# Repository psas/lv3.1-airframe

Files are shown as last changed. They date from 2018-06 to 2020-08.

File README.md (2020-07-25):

# LV3.1 Airframe
Design and testing documents related to the LV3.1 airframe.

## Table of Contents

* [license](#license)
* [cad](#cad)
* [doc](#doc)
* [sim](#sim)
* [test](#test)
* [tools](#test)

## license 
Copyright Portland State Aerospace Society 2018.

This documentation describes Open Hardware and is licensed under the CERN OHL v. 1.2.
You may redistribute and modify this documentation under the terms of the CERN OHL v.1.2. [http://ohwr.org/cernohl](http://ohwr.org/cernohl). 
This documentation is distributed WITHOUT ANY EXPRESS OR IMPLIED WARRANTY, INCLUDING OF MERCHANTABILITY, SATISFACTORY QUALITY AND FITNESS FOR A PARTICULAR PURPOSE. 
Please see the CERN OHL v.1.2 for applicable conditions.

## cad
All the computer aided design (CAD) files involved in the airframe is in this folder. Details of each folder in the directory can be found in the readme section of this directory. Most of our CAD modeling here is done and saved as solidworks files

## doc
This directory contains all the files documents regarding airframe, specifically documentation for layup processes. 

## sim
This directory contains all the simulations for LV3.1, such as rocket simulations.

## test
This directory contains all the testing data for LV3.1, such as any axial load tests performed.

## tools
This directory contains all information regarding generic tooling we use for LV3.1.

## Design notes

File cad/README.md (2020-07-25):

## CAD
This directory contains all our computer aided design (CAD) files. This includes parts, assemblies, drawings, and STEP files. Below is a listing of all the folders in this file and a short description on what they are for. 

* Commercial off the shelf components (COTS)
  - These files are all manufactured provided and not owned by PSAS, however it is in the repo to help clarify PSAS designs.
* Layup templates
  - Templates made to assist in cutting appropiate carbon fiber and nomex layers for modules B and C to aid in the layout process. Design journal can be found [here](https://docs.google.com/document/d/1Os_mgdvX-xlpNA5_TTuyKTH5s2XwF5QlSnMKPRlPtjE/edit?usp=sharing).
* Build
  - Where we put our files before they get machined as an easy place to go to when we want to check what our current physical parts look like. Organizes both the STEP and technical drawings. 
* Bulkheads
  - Directory where all the files related to the bulkhead are. A bulkhead is a dividing barrier between modules. A design journal for the bulkhead can be found [here](https://docs.google.com/document/d/1OEyzK1N2RJoIQbxRXQRS35BUAtLPPHPcPFbIrotuAhM/edit?usp=sharing).
* Coupling
  - Directory which contains all the files regarding to the LV3.1 coupling system used to connect the LV3.1 modules together.
* Fincan
  - Directory contains files describing the fin cannister, such as the bracket for the layup jig, the layup rig. Also includes images. 
* Fins
  - Directory containing all the files regarding our fins.
* Modules
  - Directory containing all files regarding our modules, including composite inner and outer sleeves, coupling examples, and our module rings.
* Nose
  - Short for nosecone, this directory has all the soldiworks files and PDFs contain files describing the LV3.1 nosecone. 
* Passthrough
  - Directory containing files for the passthrough ring for our rocket. This is a module where all the camera mounts will be.
* Rail mount
  - Directory containing files deccribing the system that mounts the rocket to the launch rail.
* Templates
  - Drawing templates (solidworks).
* Thrust flange
  - The thrust flange is the flange that the motor of the rocket will rest against. 
* Airframe bracket jig
  - Step file for the airframe bracket jig.

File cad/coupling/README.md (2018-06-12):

# Coupling System
This directory contains files which define how the LV3.1 modules couple together.

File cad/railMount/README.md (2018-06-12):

# Rail Mount
This directory contains files describing the system that mounts the LV3.1 airframe to the launch rail.

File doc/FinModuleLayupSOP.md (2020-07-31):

# Materials
* Popsicle sticks
* Wax paper
* Epoxy (proglass)
* Stirring Cups (BIG ONES)
* One (small) clamp
* Shop towels
* Gloves
* Isopropyl alcohol
* Hex wrench - 4mm or No. 6
* Foam
* X-acto kit
* Scissors
* Sharpie
* Kapton tape
* Masking tape
* Sand paper (600 grit)
* Spray bottle of water (past day 1)
* Sandbag
* Acrylic
* Abrasive Cleaner(Orange Bottle)
* Scale

# Day One
## Calibration and Prep
1. Sand all inner surfaces of the brackets
2. Find the largest seam on the module (if one exists).
3. Pick the closest bulkhead clamp screw hole.
4. Put module on the rig.
5. Put a sandbag inside the module, about in the middle, to weigh the module down during the process.
6. Using a black sharpie (choose any color, but make sure to use that color when I say black), mark a line on the end of the ring in-line with the arc clamp hole chosen.
7. Rotate the module two bulkhead holes clockwise, mark a line on the end in-line with this hole with a red sharpie (any color other than the one you used before).
8. Repeat step 4, alternating black and red sharpies until you make it back to the first line.
 * The idea behind this is to indicate that the black lines are where the fins line up, and the red lines are used to line up the module with the notches on the jig.
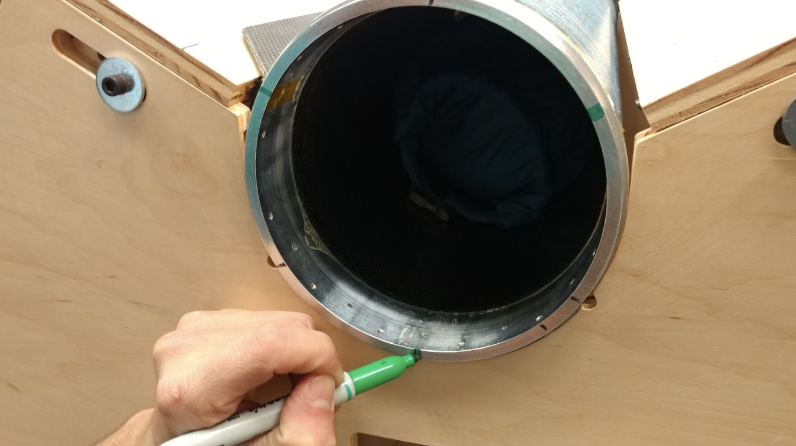
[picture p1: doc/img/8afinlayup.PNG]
 
9. Line up the inside edge of the ring with the inside edge of the front of the rig.
 * The idea is to line up the trailing end of the bracket with the inside edge of the ring module.
10. Line up two of the red lines with the notches on the rig.
  
11. Stick double-sided foam tape on the curved surface of the inside corner of a fin bracket.
12. Press the inside corner on the downward facing edge of the alignment surface of the rig, aligned with the inside edge of the module ring. This end is the bottom of the rocket.
13.Apply kapton tape around all outer module ring surfaces.
14. Move the alignment surfaces so the bracket is lightly pressed up against the module.
15. Draw a line on the module along the bottom edge of the bracket.
  
16. Back the alignment surface off and remove the module
17. Apply wide kapton tape directly underneath the marked line.
18. Tape a sheet wax paper on top of the existing kapton tape.
  * Make sure the wax paper is long enough to wrap around the bottom of the module.
19. Tape down all other edges of the wax paper.
20. Apply more wax paper as needed to span the entire length of the marked line/to wrap around the bottom of the module.
21. Reinsert the module into the jig.
22. Make sure that the module is clamped to the jig.
23. Sanity check! Make sure that the fin bracket doesn’t overlap with kapton tape.

## Layup:
24. Measure out a total of 100 g (50 of A and 50 of B) of epoxy for all surfaces. Instructions for epoxy on bottle.
  * Epoxy will get a little cloudy when fully mixed
25. Apply epoxy to the concave surface of the bracket.

26. Using the alignment surface, press the epoxied bracket onto the module where it was aligned before.
27. Hold a long piece of acrylic onto the curved surface of the bracket, underneath the alignment surfaces.
28. Firmly and evenly screw down the alignment surface bolts onto the piece of acrylic.

29. Wait at least 24 hours for curing.

# DAY 2/DAY 3/DAY 4:
## Calibration and Prep
30. MAKE SURE YOU HAVE GLOVES ON WHEN TOUCHING THE BRACKETS
31. Sand both faces of the fin, approximately the width of the fin backet, using water and sandpaper. Clean with IPA.
32. Carefully separate the alignment surface from the bracket. (Be careful taking out the module.)
  * Use a wedge of some sort to separate the foam tape from the alignment surface if necessary.
33.Remove the foam tape completely from the bracket.
34. Apply double-sided foam tape along the inside faces of TWO brackets.
  * For Day 4, it is in fact, only ONE bracket. Remove non-used alignment surface.
35. Stick the brackets on both alignment surfaces, aligning the brackets the same way as in step 9, but do not press down fully yet.

36. Rotate the module 120°. 
  * Line up the red line with the notch on the rig.
  * The orthogonal surface of the laid-up bracket should be facing downward and slightly above the new bracket.
  * For Day 3 and 4, the module will need to be taken off the rig to rotate
37. Repeat steps 10 through 16 for both sides.
  * Sandwich a fin between two brackets

38. Mark front end of fin on module (as reference)
39. Put Kapton tape along the module, the Kapton tape should be right underneath where the bracket goes
40. Tape a sheet of wax paper on top of the existing kapton tape.
  * Day 2: Make sure the wax paper is long enough to wrap around the module fully between the lines of kapton tape.
  * Day 3/4: Just let the wax paper dangle.
  * Day 4: Only one side is needed.
41. Tape down all other edges of the wax paper.
42. Apply more wax paper as needed to span the entire length of the marked line/to wrap between the lines.
43. Wipe down the exposed faces of the module with isopropyl alcohol 
44. Tape the top face of the fin with masking tape so you move the fin up and down like a flap so the fin stays in the same position.

## Layup:
45. Rotate the module slightly back, giving enough clearance between the old a new bracket for a fin.
46. Measure out a total of 100 g (50 of A and 50 of B) of epoxy for all surfaces. Instructions for epoxy on bottle.
  * Epoxy will get a little cloudy when fully mixed
  * Somewhat less is needed is needed for Day 4
47. Apply epoxy to the exposed surfaces of the brackets.

48. Put bracket into position onto alignment surface
49. Apply epoxy to new bracket mating side of fin
  * Have a shop towel soaked with iso ready to wipe off dripping epoxy

50. Fold fin down onto new bracket and hold firm
51. Epoxy remaining side of fin and the old bracket mating face

52. Rotate fin can until flush with fin
53. Press alignment surface down onto module
54. Line up edges of old to new bracket
55. Sandwich fin as firmly as possible between the two brackets
56. And clamp! 

57. Screw in the sides with the hex wrench
58. Cinch the bracket down with the strap and ratchet. 
59.Seal any extra space between the bracket and the fin with leftover epoxy
60. Put the acrylic on the bottom of the curved part of the bracket and press firm with screws
  * Put wax paper underneath the acrylic 
61. Repeat Day 1 layup for the second bracket
  * Not needed on Day 4

62. Wait at least 24 hours for curing.

# Post Layup Touch Ups:
* Fill any gaps between bracket and fin or bracket and module with epoxy
* Sand, sand, sand
* Clean with isopropyl

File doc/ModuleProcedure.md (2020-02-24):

---
Title: Composites Layup Procedure
Date: \today
Author:
  - Joe Shields
  - Leslie Elwood
  - Alex Farias
Revision: Version 3.1
Revised by:
  - Gabe Paris
Fontsize: 12pt
Documentclass: article
Geometry: margin=0.75in
Numbersections: true
Toc: true
Pagestyle: plain
Output:  
  pdf_document:
    latex_engine: xelatex
---
# Introduction
This is the procedure to make a cylindrical module specifically for the Launch Vehicle (LV) 3.1. If you find any steps that are unclear, erroneous, unneccessary, or need improvement, please [add an issue for it on this repo](https://github.com/psas/lv3.1-airframe/issues).

This procedure takes about 5 hours if you have three people working on it, not counting the 5 hour cure cycle. If you're following this procedure for the first time, it will probably be closer to 7 or 8 hours. If you *really* know what you're doing, one person can do it, but it's not nice to make one person work for 10 hours straight. If you're trying modifications to this procedure, it's a good idea to do so on a smaller mandrel with no coupling rings, since that takes off a lot of the time.

The composites training video can be found here [link coming soon], and it goes over the process of making these modules. If this is your first time following this procedure, please watch the video first.

## Materials
### Consumables
1. [Orca skin](http://www.fiberlay.com/upload/techd-2522041-252204_OrcaSkin_Data.pdf)
1. [Orca seal](http://www.fiberlay.com/upload/techd-252203-252203_OrcaSeal_Data.pdf)
1. Shrink tape
1. Non-perforated release film
1. Vacuum bag sheets
1. Vacuum bagging tape ("goop tape")
1. Vacuum bagging breather material
1. 320 grit sandpaper
1. 600 grit sandpaper
1. 1500 grit sandpaper
1. Acetone
1. Powderless nitrile gloves
1. Blue shop towels
1. Kapton tape or flash tape
1. 1 whole 3M AC-130 pre-treatment solution
1. Separation wax

### Layup Pieces
1. Prepreg carbon fiber (Satin weave is preferable. Anything but unidirectional will do. We use Cytec BMS-8-297 3K-70-PW TY4 CL2, which is the big yellow roll in the EB 480 freezer.)
1. Structural adhesive (We use Cytec's Meltbond 1515-3M, which bonds to CF, nomex, and aluminum. We know that 3M's AF-126 DOES NOT WORK.)
1. Two (Generation 2) Aluminum Coupling Rings
1. 12 aluminum coupling ring arc clamps
1. 1/4" thick over-expanded nomex honeycomb
1. An aluminum mandrel (6.0" OD!)

### Tools
1. Vacuum pump (we use a venturi pump)
1. Air hose
1. Insulated gloves (gardening gloves will work)
1. Utility knife
1. XActo knife (Optional, but helpful for finer trimming.)
1. Scissors
1. Mandrel-to-ring screws (size)
1. A small piece of acrylic (Popsicle sticks will work as well, albeit more difficult)
1. Material templates and weights

# Preparation
The following steps can be done in parallel. If you have the space and the people, this is recommended to save time.
## Mandrel Preparation
#### Mandrel Cleaning
1. Put on powderless nitrile gloves.
1. Use a piece of acrylic or a popsicle stick to scrape away any chunks of epoxy or adhesive currently on the mandrel from the previous layup.
1. Wet sand the mandrel with 320 grit paper to remove the epoxy and adhesive from the previous layup.
1. Wet sand the mandrel with 600 grit paper, removing the marks from the previous sanding.
  1. The sanding direction can be alternated (that is, axial v.s. radial) to better identify any spots that were missed, but this is optional.
1. Wet sand the mandrel with 1500 grit paper, removing the marks from the previous sanding. You want the mandrel to be as smooth as possible before continuing.
1. Put on fresh (as in change to a new pair) powderless nitrile gloves.
1. Wipe the mandrel with acetone and a blue shop towel to clear the sanded epoxy and metal dust until the towel comes back clean.
1. Relocate the mandrel and the composites table to a space with good ventilation. We normally use a spot on the north end of the first floor of EB where there is a set of double doors for ventilation.

#### Mandrel Conditioning
The figure below shows the waxed mandrel along with a container of Orca skin and Orca wax. This should be done in an area with good ventilation because the wax chemicals are very potent.

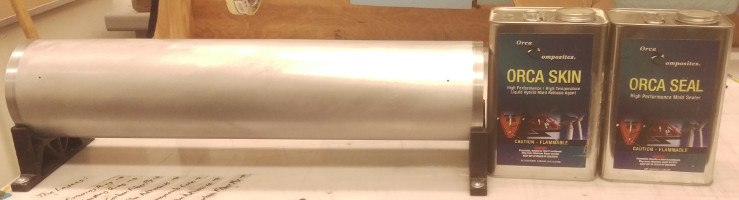
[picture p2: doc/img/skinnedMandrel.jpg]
The waxed mandrel on the preparation table, along with a container of Orca Skin and Orca Seal


1. Put on (Brand new!) powderless nitrile gloves.
1. Place the freshly sanded mandrel to be conditioned on the mandrel holders.
1. Fill mandrel threaded holes with separation wax.
1. Apply 2 coats of Orca Seal. For each coat, complete the following:
   1. Shake the container of Orca seal to mix the wax and then unscrew the lid.
   1. Apply some Orca seal to a blue shop towel by *carefully* covering the opening of the container and briefly inverting.
   1. As lightly as you can and as evenly as you can wipe the wax onto the mandrel. Usually the first wiping motion of the towel will be thick and visible on the mandrel; this is common. If you are able to more evenly distribute the thicker streak, do so, otherwise it will be fine.
   1. If there are any chunks of wax, carefully remove them with a shop towel.
   1. Let the coat of wax dry a little before procedding with the next coat. This drying process can be sped up with a heat gun.
1. Apply 7 coats of Orca skin the same way, with 10 minutes between coats. This process can be sped up with a heat gun, but you want to make sure the previous coat is as dry as possible, otherwise the wax will streak when you try to work with it.
1. Wait approximately 1 hour for the wax to completely dry and set.

## Coupling Ring Preparation
#### Coupling Ring Cleaning and Deoxidization
1. Put on powderless nitrile gloves.
1. Wet sand the adhering surfaces of the rings with 320 grit paper (3 passes circumferentially).
1. Put on fresh powderless nitrile gloves.
1. Clean all surfaces with acetone and a blue shop towel to remove metal shavings.
   1. We change gloves before this step to prevent any dust that stuck to the gloves from falling back onto the mandrel.

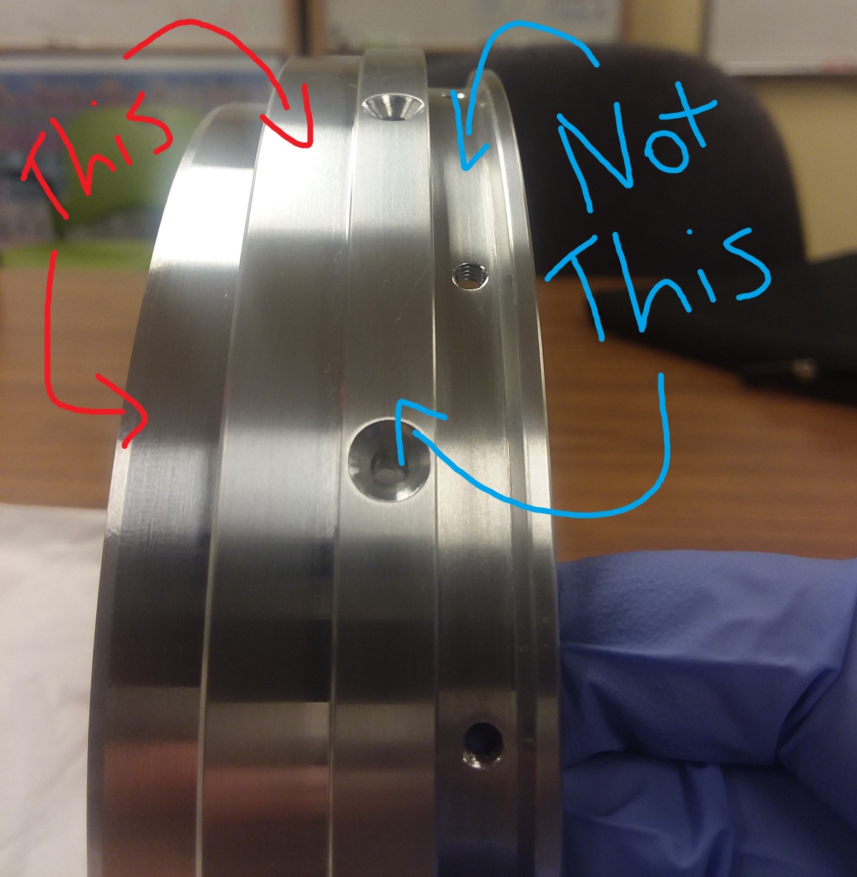
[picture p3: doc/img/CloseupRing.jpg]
Closeup of the coupling ring surfaces


#### Coupling Ring Conditioning
1. Put on fresh powderless nitrile gloves.
1. Mix the 3M AC-130 pre-treatment solution according to the instructions within the kit.
1. Continuously apply the anti-galvanic 3M AC-130 to the adhering surfaces for 3 minutes with a brush (like a watercolor painter, slowly rotating around the whole adhering surfaces-- but do so for 3 minutes, rather than a certain number of rotations).
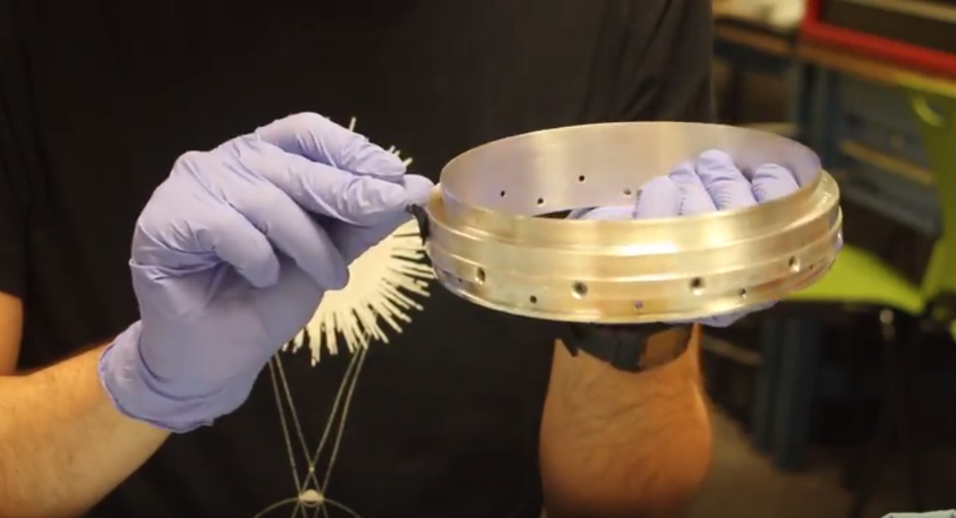
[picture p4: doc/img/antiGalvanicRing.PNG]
Closeup of the anti galvanic process with a brush

1. Take care not to touch the adhering surfaces from this point on because it will contaminate the anti-galvanic and you will have to re-apply it.
1. Wait for 10 minutes to allow the solution to dry.
1. Put on fresh powderless nitrile gloves.
1. Apply the anti-galvanic solution again.
1. Relocate the composites table and the rings to a well-ventilated area if it has not been already.
   1. It may be worth waiting until everything is ready to be waxed before moving the table. This reduces risk of dropping or damaging the rings while moving by hand.
1. Wait for 60 minutes to allow for everything to dry.
1. Apply 1 coat of Orca seal to the innermost surface using the same method as with the mandrel.
1. Apply 3 coats of Orca skin to the innermost surface, waiting 10 minutes between coats.
1. Wait for 60 minutes.

**IMPORTANT: _If the adhering surface of the rings is disturbed, it will affect the performance of the completed module, so take care to avoid touching these areas because you will have to clean the adhering surface and re-galvanize it._**

## Cutting Films and Fabrics
These steps are best done in advance or while you are waiting for the anti-galvanic juice to chooch and the final layer of mold release to dry.

#### Pieces to Cut:

Cut the following layers using the General Template Use instructions below. The format for the templates is:
<p align="center">
[Template]-[Size]-[Layer Identifier]
</p>

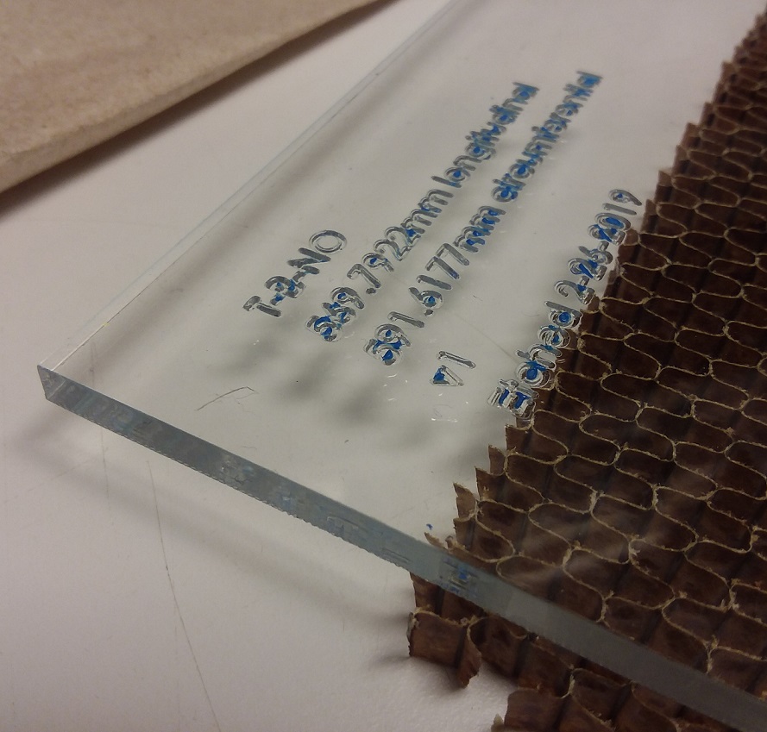
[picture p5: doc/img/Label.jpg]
Closeup of the template label
The template code can be found in the corner of the template, as shown here:  

The size part of the code refers to the mandrel you are using. The "X" is to be replaced with A, B, or C, where A is the smallest mandrel (image below). The layer identifier indicates if the piece is:
1. An inner or outer layup piece (I or O)
1. The material being cut (C for carbon fiber/adhesive, NO for nomex)

The materials that need to be cut are:

| T-X-IC | T-X-OC | T-X-NO |
|---|---|---|
| Inner Release Film\* | Mid Adhesive | Nomex |
| Inner Carbon Fiber | Outer Carbon Fiber A | |
| Inner Adhesive | Outer Carbon Fiber B | |
| | Outer Adhesive | |
| | Outer Release Film\** | |

<sub>\*- Remove 3/4 inches from length</sub><br/>
<sub>\**- Add 3 inches to length</sub>

Mandrel sizes:
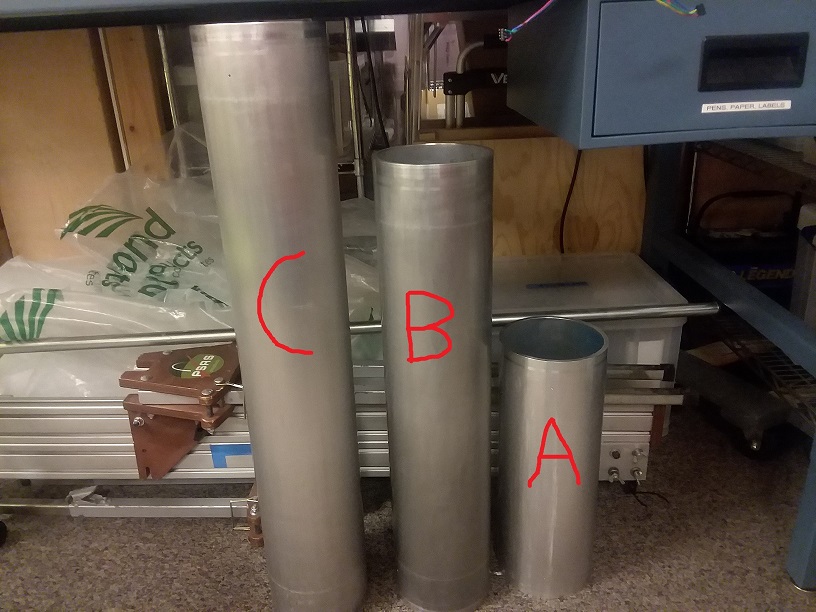
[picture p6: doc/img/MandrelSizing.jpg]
Image of the mandrels from largest to shortest


It will be useful to label each of the layup parts so you don't accidentally place the wrong layer in the wrong spot during the layup process. You can write which layer it is in Sharpie on the protective backing of the layers.

Additionally:

1. Cut two strips of adhesive with dimensions 1/4" by 20" to apply to each coupling ring. Make sure they are no wider than 1/4".
   1. This can easily be done by placing the edge of a template on a straight-cut piece of adhesive and using the depth gauge of a pair of calipers to tweak and check the width of a strip.

#### General Template Use

1. Select the appropriate template for the desired film or fabric using the table above.
1. Lay the film or fabric over the plastic surface of the work bench.
1. Place the template over the film or fabric.
   1. When cutting the overexpanded nomex honeycomb core material, make sure the template is oriented correctly! The overexpanded cells only bend in one direction. Make sure the template is oriented such that the nomex will be able to bend around the cylinder.
   1. You should only be cutting single rows of cells (don't cross from one row to another).

| Nomex Bending the Right Way | Nomex Bending the Wrong Way|
|:---:|:---:|
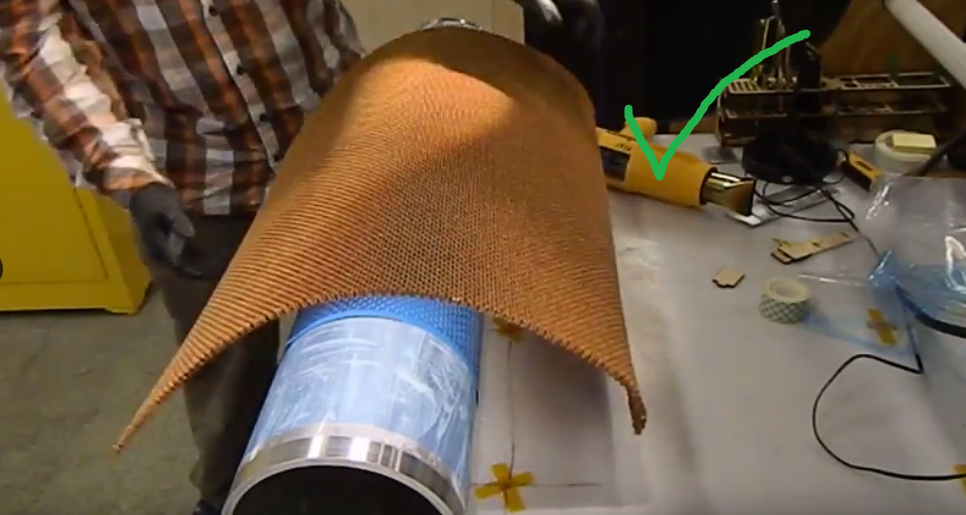
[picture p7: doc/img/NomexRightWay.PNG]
Correct way to lay nomex
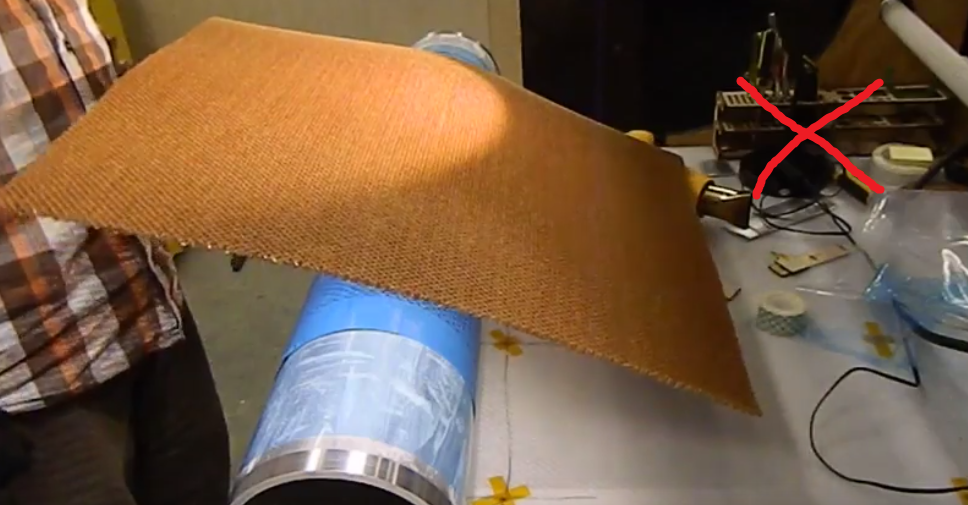
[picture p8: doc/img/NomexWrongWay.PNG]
Wrong way to lay nomex
| | |

1. To cut the carbon fiber, it works well to place the corner of the template on the corner of one of the cells (you will have to remove one of the layers of peel ply). The template can then be rotated such that it perfectly lines up with the rows and columns of the fabric. NOTE: this doesn't work with fiberglass.
   1. Make sure the area being cut does not intersect bad portions of the CF.
1. While one person moderately presses down on the template, another person should cut along the edges with a utility knife, pressing hard enough to cut through the material.
   1. It also works well to place weights on the templates while cutting, especially when cutting the adhesive and if you are working by yourself.
1. Lift up the outside portion of the cut before removing the template to check that the cut is complete. If it isn't, slice the remaining material.
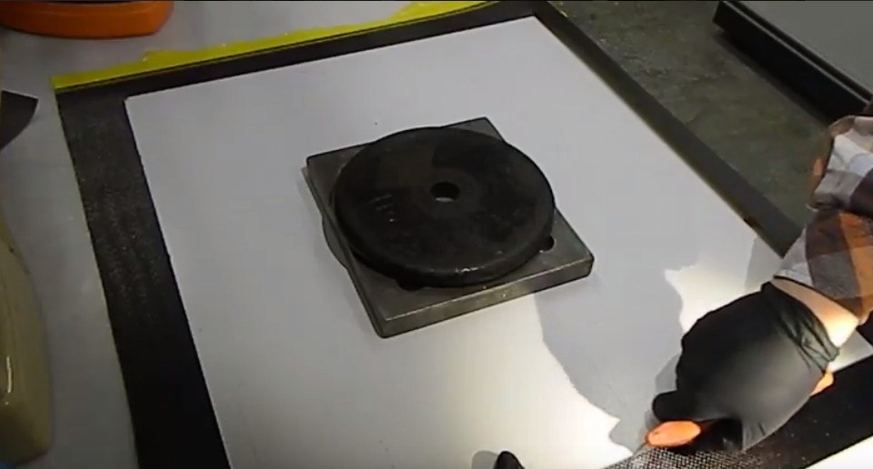
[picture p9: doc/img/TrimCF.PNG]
Use of template for CF and Adhesive


# Assembly
These steps must be done in series. The layup table really only accomodates 2 or 3 people, so just switch out people as appropriate.

## Step 1: Hardware Assembly &amp; Final Conditioning
What follows is the general procedure for assembling all prepared pieces.

**_IMPORTANT: If the adhering surface of the rings is disturbed, it will affect the performance of the completed module. Take care to avoid touching these areas because you will have to clean the adhering surface and re-apply the anti-galvanic treatment._**

1. Put on fresh powderless nitrile gloves.
1. Without touching the waxed surface of the mandrel, slide the coupling rings onto the mandrel.
1. Screw the coupling rings to the mandrel. It works best to place the mandrel upright with one person sliding down the coupling ring from the top and another person fastening the screws.
1. Place the mandrel onto the mandrel holders.
1. Place the arc clamps on the connecting side of the rings, 6 on each ring, and secure with kapton tape.
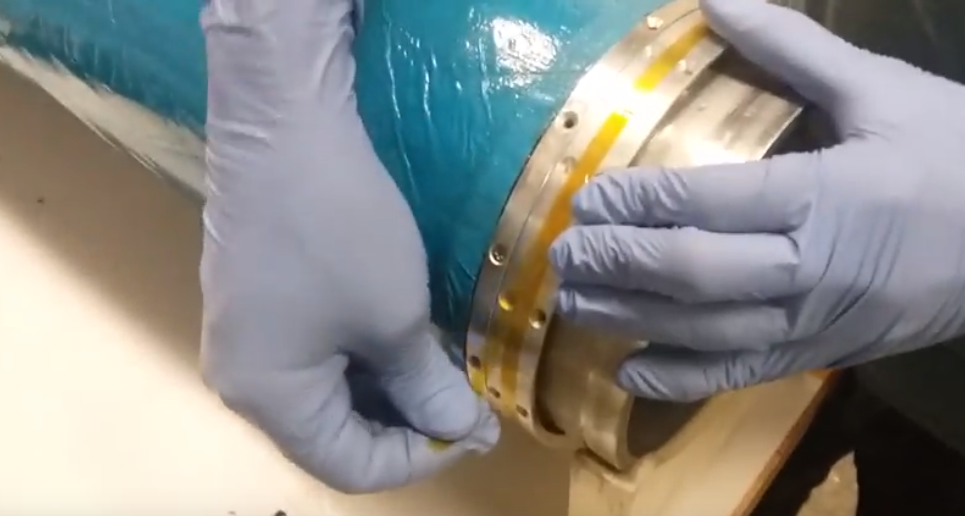
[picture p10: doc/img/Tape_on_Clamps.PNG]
Coupling ring with arc clamp
  
   1. The easiest way to do this is by placing an arc clamp in position and taping it to the previous arc clamp, but if there is an easier way for you, then do that.
   1. Put a couple of screws in the bracket holes to keep the ring of brackets in place. This comes in handy later.
1. Cover all the screw heads with kapton tape. This will prevent the epoxy or adhesive from flowing into them. Make sure the tape is as secure as possible; this can be done by covering the screw heads with more than one layer of tape.

## Step 2: Layer Layup (L<sup>2</sup>)

**_IMPORTANT: Each layer you apply will overlap itself. Try to make sure the overlapping sections of each layer is in a different location. Make sure consecutive layers have at least 90 degrees of separation between their overlap regions (basically, don't start each layer in the same spot)._**

We will be using the **Special Peel Technique** for each of the materials that has a protective peel ply layer on it. Note that this applies _after_ the material has been wrapped onto the mandrel. This ensures that the material (CF or adhesive) does not fall off by accident while removing the protective layer, as well as prevents the material from falling off the mandrel and ruining it with debris. This technique is:

1. Peel the overlapping section of the adhesive back _off_ of the mandrel while someone holds the underlapping end secure. This is to make room for the next step.
1. Start peeling the protective backing, starting from the underlapping end and proceeding circumferentially.
1. Roll the overlapping end back onto the mandrel.

The order proceeds as follows:
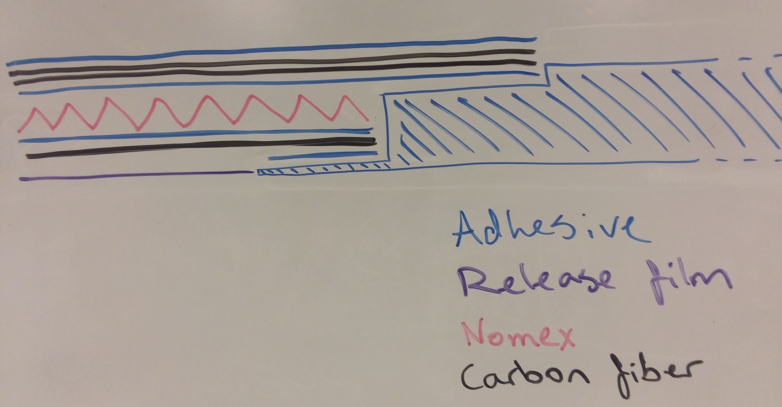
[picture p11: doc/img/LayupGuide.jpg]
Drawing depicting the order of materials in the layup


##### Release Film:
1. Wrap the Mandrel with the inner release film piece. It should span the entire molding surface of the mandrel and either not overlap with the coupling rings, or be tucked under the knife-edge of the rings. This is to prevent the module from sticking to the mandrel, but we want it to stick to the rings!

##### Adhesive Strips:
1. Lay the adhesive strips onto the lower adhering surface of each coupling ring (aka the knife edge). Make sure the strips are no wider than 1/4". The extra 1/8" of flange is to prevent the adhesive from flowing into the mandrel when hot.

##### Inner Carbon Fiber:
1. Remove one of the protective backing layers from the inner carbon fiber layer piece.
1. Lay this CF piece onto the mandrel, exposed side down. It should cover the release film and overlap the adhesive strips completely, butting up flush against the step of the rings (see below). The CF should overlap itself by about an inch. Don't worry too much about small wrinkles, they will be automatically smoothed during the cure cycle, but do try to smooth larger wrinkles and folds. _Do not tug or pull on the CF in an attempt to remove wrinkles._ If you need to remove large wrinkles, re-lay the CF instead.
1. Peel the remaining protective peel ply backing from the CF using the **Special Peel Technique**.

##### Innermost Adhesive Layer:
1. Peel the _paper_ protective layer from the inner adhesive layer piece.
1. Lay this inner adhesive piece over the CF, exposed side down. Rotate the mandrel while someone holds down the underlapping end.
1. Peel the remaining orange peel ply backing from the adhesive using the **Special Peel Technique**.

##### Nomex Layer:
1. Lay the overexpanded nomex honeycomb core over the mandrel. It works best to start at the seam (_not_ the ring edge) so the cell compression is more evenly distributed. Use a heat gun to tack the seam of the nomex into the underlying adhesive.
1. Firmly press the nomex into the adhesive. Be careful not to overheat the nomex; if it starts to notiseably warp, it's warm enough, and if it starts to darken, you got it too hot.
1. Go to the side of the nomex opposite the tacked part and use a heat gun to secure that end. You should have bowing on the untacked sides, like a bean.
1. Tack the remaining sides and make sure there are no "bubbles," aka untacked areas, in the nomex layer,

##### Mid Adhesive Layer:
1. With the nomex now affixed to the inner adhesive layer, remove the paper backing from the next piece of adhesive film.
1. Lay this next piece up over the nomex, with the newly exposed side facing inward, and rotate the mandrel while someone holds down the underlapping end.
1. Peel the remaining protective backing from the adhesive using the **Special Peel Technique** and ensure the adhesive layer is tight around the nomex.
1. If the adhesive layer is not sticking:
   1. Secure it with kapton tape. This can be done by folding the end of a piece of kapton tape into itself to create an easy-peel tab. Place the kapton tape so that the easy-peel tab is on the overlapping side, transitioning to the underlapping side.
   1. Hit it (very) lightly with a heat gun. **Avoid the part with the kapton tape!**
   1. **Do not touch the adhesive until it is cool!** Wait at least 15 minutes before handling it, otherwise it will stick to your gloves.
   1. Remove the kapton tape after the adhesive is solid again.

##### First Outer CF Layer:
1. Remove one of the protective backing layers from the first outer carbon fiber piece.
1. Lay this CF piece into the mandrel. Take care not to tug on the carbon fiber; the shrink tape will remove any wrinkles better than you can. Take care that the material does not extend over the lip of the coupling rings.
1. Use the **Special Peel Technique** to peel the remaining protective backing off of this CF layer.

##### Second Outer CF Layer:
1. Remove one of the protective backing layers from the second outer carbon fiber layer piece.
1. Lay this CF piece into the mandrel. Like with the other pieces of carbon fiber, do not tug on or pull the material, and make sure that the material does not extend over the lip of the coupling rings.
1. Use the **Special Peel Technique** to peel the remaining protective backing off of this layer of carbon fiber.

##### Outermost Adhesive Layer:
1. Peel the _paper_ protective layer from the outer adhesive layer piece.
1. Lay this newly exposed surface against the carbon fiber layer. Rotate the mandrel while someone holds down the underlapping end. Take care that it does not extend over the lip of the coupling rings.
1. Peel the remaining protective backing from the adhesive using the **Special Peel Technique**.

##### Outer Release Film:
1. Wrap the entire layup with the outer release film piece. This is to prevent the module from sticking to the vacuum bags and shrink tape.
1. **IMPORTANT:** If the shrink tape you are using has release coating on it, apply the outer release film OVER the shrink tape (which is applied in the next step). This will result in a better surface finish. Double check whether the shrink tape has a release compound on both sides or just on one, and make sure the side with release compound faces inward toward the previous layer. If you have read the procedure and catch this note, mention it to the overseer of the layup session in a discrete manner (that is, do not let anyone else know that you found this. It's a game).

## Step 3: Shrink Tape
1. Arrange the shrink tape on a spool so that the outer surface may be easily applied to the layup (underhand from the spool; overhand onto the layup). This setup puts the mandrel between you and the spool.
1. Set up a workbench lamp such that it illuminates the layup.
1. Use kapton tape to fix the shrink tape into the arc clamps. Use lots of tape to fix them in place (one suggestion is to do 2-3 loops around the rings with tape). If it comes loose, the layup will be ruined. If the arc clamps are secured well, they will serve as a strong anchor for the shrink tape.
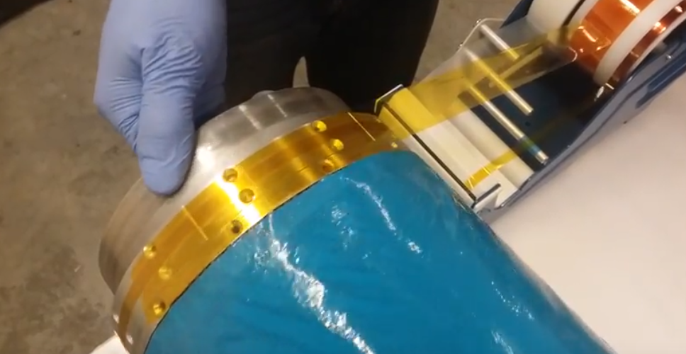
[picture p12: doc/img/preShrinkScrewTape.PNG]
Tape down screw holes before shrink tape

1. Use your dominant hand to tension the shrink tape against the layup.
1. Use your off hand to rotate the layup, wrapping the shrink tape around it. If you are working in groups, one person can rotate the mandrel while the other applies the tape. In this case, the off hand can be used to ensure the tape applies evenly.
1. Adjust the position of your dominant hand such that each turn of the shrink tape overlaps the previous one by 75% (one quarter offset). This should result in the appearance that the surface is covered in a single sheet of double-thick shrink tape. If there are any gaps or triple-overlaps, you must roll the layup backwards and redo those sections. You are basically trying to align the edges of the shrink tape together. Defects due to misalignment of the shrink tape will result in ribbing in the final product.
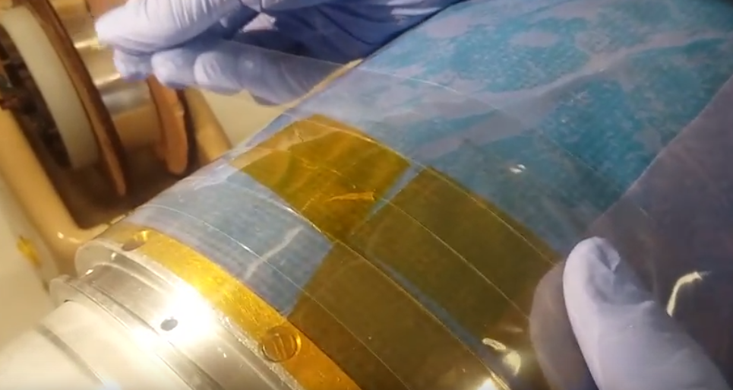
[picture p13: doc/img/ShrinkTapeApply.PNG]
Image of offset of shrink tape
    
   1. Note: there will be ribbing regardless of what you do, but this step minimizes how prominent that ribbing is.
1. Every 3 or 4 rotations, add a piece of kapton or flash tape to save your progress, and adjust the positions of the lamp and tape spool to your convenience as you go. The lamp is used to illuminate the are where you are working and make the overlapping process easier to see.
1. When you reach the end of the opposite coupling ring, repeat the wrapping process until you end up back where you started (basically go down and back the length of the module). This will create a double layer of shrink tape.
1. Cut the shrink tape and securely fix it to the ring of clamps using kapton or flash tape.
1. Add 3 strips of kapton or flash tape that span the entire length of the module to fix the shrink tape against nudges during the vacuum bagging process.
1. If you are using perforated shrink tape, add a layer of non-perforated rerlease film to the outside of the layup, using kapton or flash tape to hold it in place.
   1. If you don't do this, the module will end up with "goosebumps," which make the shrink tape much harder to remove and the module much harder to sand.

## Vacuum Bagging
After adding the finaly layer of release film, the layup is ready to be vacuum bagged. An image of how the module should look at this point is provided below. Mandrel holders are not requires after the shrink tape has been applied. This part is done in the room with the oven.

**Note:** If you are freezing the module to cure for another time, follow the process below up to step 9. Seal all but a couple inches of one end to allow access for the vacuum hose.

1. Lay the breather material ("diaper") over the mandrel.
1. Secure the breather material with either kapton tape or flash tape. Note that this tape sometimes does not like to adhere to the breather material, so use longer strips of tape to keep the material in place. If there is extra breather material, it can be trimmed or tucked into the ends of the mandrel.
1. Cut the vacuum bag material to the size of your mandrel. It is better to be larger than the mdule and trim down later. Note that the vacuum bag material has two layers; these layers can be separated after the material is cut.
   1. **Important:** Both sheets of vacuum bag material need to be the same size. If you try to make one bag smaller, it will be _extremely_ difficult to tape the ends together. It has been tried, 0/10 would recommend.
1. Form two tubes that are 7-8 inches in diameter using the following process:
   1. Join the longer seams of the vacuum bag sheet together using the yellow vacuum bag tape ("goop tape"). This tube should be longer than the mandrel by at least 12 inches on both sides. Again, you can always trim down later.
   1. Gently pinch any air channels out of the goop tape. This can be done by holding the air channel between two fingers and wiggling the material back and forth until the goop tape fills the gap.
   1. You should have two separate tubes, each with two open ends and a sealed long edge.
1. With the mandrel on its side, take one of the tubes and push it through the inside of the mandrel. Set the mandrel upright and pull the second tube over the outside of the mandrel.
1. Place the mandrel back on its side to center the bags around the mandrel. The next step will be easier if the seams of the tubes are not aligned.
1. Using the goop tape, seal one end of the inner tube to the corresponding end of the outer tube. If the vacuum bag material is the same size, this step should not be difficult, but if they are different sizes then you will have to make sure the extra length is sealed off.
1. Take care that there is no air channel formed by the overlap of the outer tube with tiself. Pinch out channels with the same process as earlier. *Everybody makes this mistake at least once!*
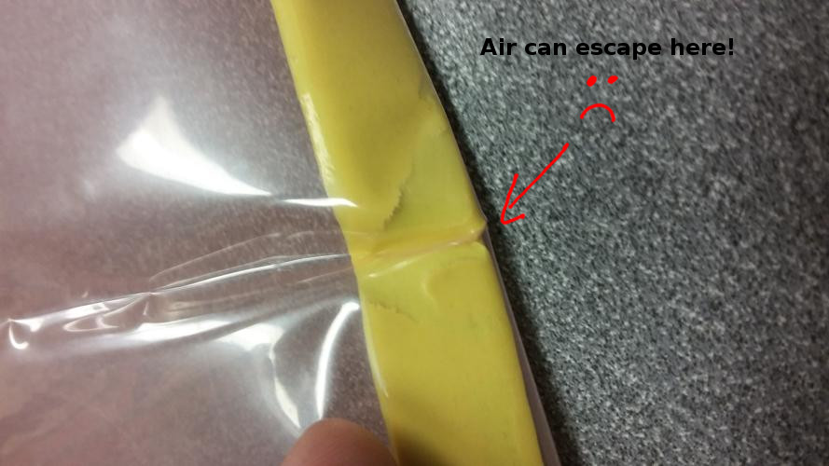
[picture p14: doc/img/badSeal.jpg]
Closeup of the bad air channels

1. Gently pinch any air bubbles or air channels out of the goop tape. This is mentioned again because it's very important.
   1. If you are freezing your module, leave room for the vacuum pump to go into the bag before wrapping the module in plastic and relocating to the freezer.
1. Cover the end of the vacuum hose with diaper material, securing it with kapton or flash tape.
1. Place the diaper end of the vacuum hose between the vacuum bag layers and near the coupling ring.
1. Carefully apply goop tape to the vacuum hose so that it may be sealed with the tubes.
1. Seal the open end of the tubes with the same process as before, and take special care to make sure the hose and tubes form a complete seal. Make sure there is no air channel formed by the overlap of the outer tube with itself.

# Curing
## Cooking
This part of the procedure can only be done in EB 480 or otherwise with an oven that reaches high temperatures.

1. Thread the vacuum hose through the hole in the oven wall.
1. Gently place the mandrel near the oven. Avoid carrying it by the module that you just assembled, because this can warp the final product; instead, carry it by the mandrel ends.
1. Attach the outside end of the vacuum hose to the venturi pump. It should already be attached to a compressed air supply, but if it isn't, then attach it.
1. While slowly turning on the compressed air supply, check the bag for hissing (this indicates a leak which must be sealed with goop tape). If the module is kept outside the oven, it is easier to move around to listen for leaks.
1. When the bag is no longer showing signs of air escaping, turn the air supply on completely and set the module inside the oven. Try to get it as horizontal as you can, but if it leans diagonally this will be ok.
1. Close and latch the oven.
1. Make sure the oven is plugged into two separate circuit breakers.
1. Make sure both relays on the side of the oven are in the “on” position. When this is done, you are ready to follow the instructions taped to the oven (image provided below).
1. Ramp up the the oven at 3°F per minute until it reaches 350°F.
1. Place the snorkels/fume hoods above the oven, open all the doors of the room, and place a fan in at least one doorway.
1. After it reaches 350°F, hold the oven at that temperature for two hours.
1. Ramp down the oven temperature by no more than 5°F per hour. Use the oven door to control this cooldown by opening it slightly for faster cooling.

| Time (min) | Temperature (F) |
|:---:|:---:|
|0:00 | 75 |
|0:15 | 120 |
|0:30 | 165 |
|0:45 | 210 |
|1:00 | 255 |
|1:15 | 300 |
|1:30 | 350 |
| -- 2 hours --| *Hold* |
|3:30 | *Cooldown* |

## Removal from mandrel

1. While the mandrel is cooling, position the mandrel holders on the composites table.
1. Once the oven has reached 100°F, open the door and slide vacuum hose into the oven, through the hole in the oven wall, using insulated gloves.
1. Remove the mandrel from the oven using insulated gloves and place it on the mandrel holders on the workbench.
1. Cut open and dispose of the vacuum bag.
1. Remove the hose, diaper, and release film from the mandrel and dispose of them.
1. Place the layup vertically on the table and slide the module up. It should easily slide off. If it doesn’t wait until it cools to room temperature. If it still does not come loose:
    1. Place four mandrel removal blocks on the floor.
    1. Place the mandrel in the blocks, using insulated gloves.
    1. Place a piece of wood on the top of the mandrel.
    1. Tap the piece of wood with a hammer to release the mandrel from the module.
    1. With one person holding the mandrel with insulated gloves, gently pull and wiggle the module off the mandrel in the direction of the male ring. Take care not to damage the module or mandrel. If necessary, run cold water through the inside of the mandrel. This will thermally shrink the mandrel, allowing it to slide off easier.
    1. If the module remains stuck, place it on a piece of plywood with the removal blocks holding it up.
    1. Place the wooden plug inside the mandrel on top.
    1. Place a 2x4 on the plug.
    1. Hammer on the 2x4 with a large weight (~50 lb) to slowly separate the mandrel and module. Stack chunks of 2x4 under the removal blocks to get more height.
    1. If you need to do this, you did something wrong with the mold release and/or release film.
1. Place the mandrel back on the mandrel holders on the workbench.
1. Remove the blue perforated release film from the inside of the module.

# Results

If done properly, this should result in a module with maybe a few thin creases from flaws in the shrink tape. Adhesive-surfaced modules should be finished with 600 and 1500 grit wet sanding. (do not submerge!)

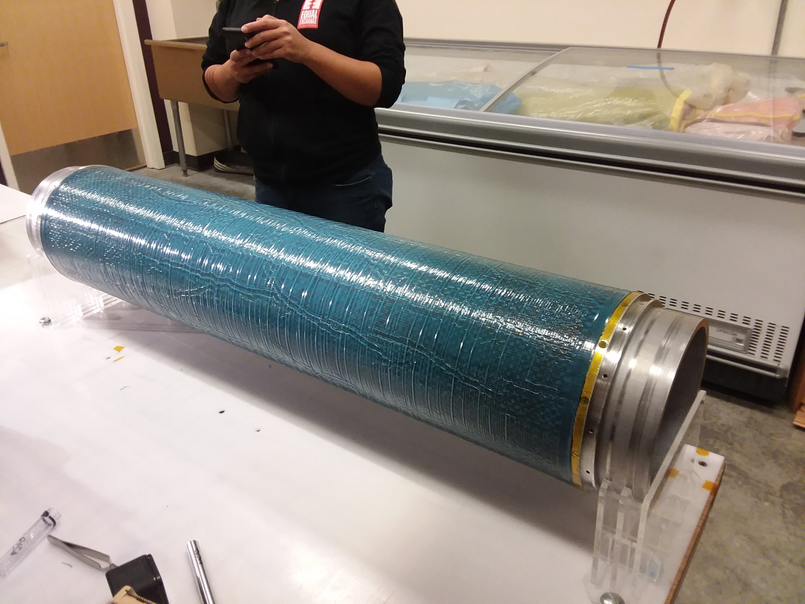
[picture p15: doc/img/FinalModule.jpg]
Final product


## (Optional) Sanding

Design note: when co-curing the outer layer of adhesive with the carbon fiber, the adhesive layer sinks into the CF to effectively sand it. The highest points of the carbon fiber are above the lowest points of the adhesive. This can be mitigated by post-curing the outer adhesive layer onto the carbon fiber. For LV3.0, it was decided that the extra manufacturing time to post-cure and fully sand a module wasn’t worth the small decrease in drag.

### Tools

1. Module sanding lathe (need pictures!)
1. BoM?
1. Electric drill (corded preferred)
1. Adhesive-covered module
1. Personal protective equipment
1. Splash goggles
1. Nitrile gloves
1. Full body splash suit (must be hooded, disposable is fine)
1. Dust mask (respirator is fine)
1. Plastic bags
1. Plastic sheeting
1. Spray bottle (water)
1. Wet-or-dry sand paper
1. 320 grit (only for post-cured or multi-layer adhesive)
1. 600 grit
1. 1500 grit

### Procedure

##### Preparation:
1. Assemble the module on the sanding lathe. (It’s not a great design and you kind of have to just figure it out each time.)
1. Lay out a sheet of plastic covering the surface and back of the layup table.
1. Put on a hooded Tyvek suit, nitrile gloves, splash goggles, and a dust mask. If you have a face shield, that will work in place of the goggles and dust mask.
1. Place the sanding lathe onto the plastic sheeting on the layup table.
1. Cover the bottom of the sanding lathe with plastic sheeting or paper bags.
1. Use a plastic bag to loosely cover the drill. Be careful to protect the vents from water, while still allowing them to breathe.
1. Tape one of the pieces of key stock that lives with the sanding lathe into the end of the keyed shaft.
1. Chuck the drill onto the end of the shaft, so that the key sits between the jaws of the chuck, allowing the drill to drive the shaft.

##### Sanding:
1. Spray down the surface of the module with water.
1. Using one hand to control the drill and the other to press the sand paper onto the module, begin sanding the module. Start with the lowest (coarsest) grit you plan to use.
1. Stand in the plane of rotation of the module, so that when the slurry flies off it gets on your suit rather than the room.
1. Control the throttle of the drill to keep the rotation slow and the pressure on the sandpaper high, but don’t stall the drill.
1. Add water and wipe away the slurry as necessary.
1. Periodically clean and dry the area you’re working on and check to see if you’ve sanded through the adhesive into the CF. If you find any black spots where this has happened, stop sanding that area and move onto the next area.
1. After the length of the module has been sanded, move to the next higher grit. If you don’t care about making the module shiny, you don’t need to bother with the 1500 grit.

##### Cleanup:
1. Remove the plastic bags/sheeting from the sanding lathe.
1. Clean the outside of the module with water and paper towels.
1. Move the sanding lathe to a clean location.
1. Gather up and dispose of the plastic sheeting.
1. Clean any stray spills.
1. Disassemble and dry the sanding lathe.
1. Gather up and dispose of your disposable PPE. Clean whatever isn’t disposable.

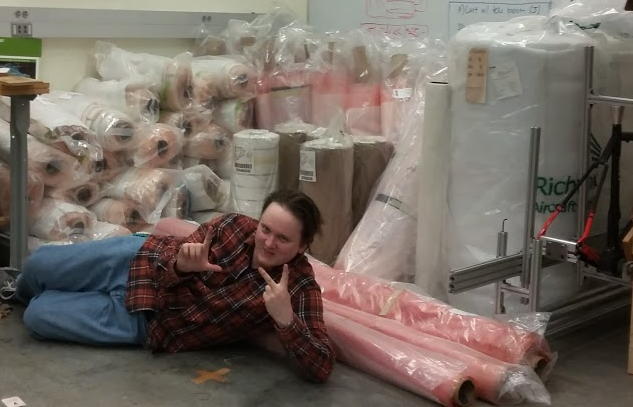
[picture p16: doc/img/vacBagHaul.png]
Joedang


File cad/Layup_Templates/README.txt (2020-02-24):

These are layup size templates for the multiple layers involved in a module layup. These were created to assist in cutting the appropriate carbon fiber and nomex layers for modules B and C. The naming convention follows T-X-YY, where T stands for template, X is the module type (currently B or C), and YY follows 
	Inner carbon fiber layer - IC
	Nomex - NO
	Average of two outer carbon fiber layers - OC

The layup template design journal can be found in PSAS Shared Drive > LV3.1 > Sub Projects > Airframe > Modules > Layup Template Design Journal

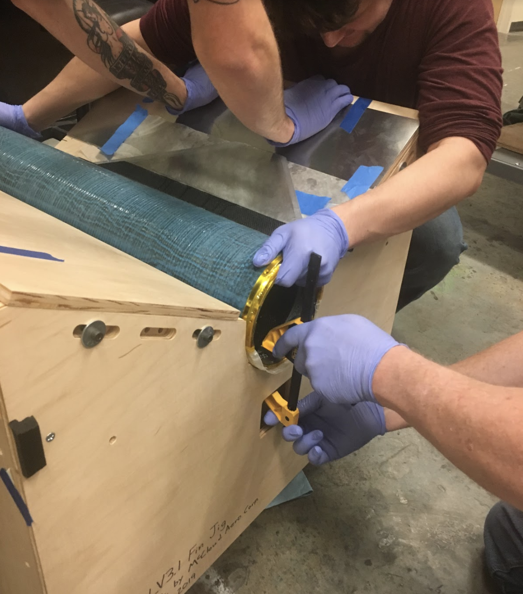
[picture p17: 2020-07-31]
doc/img/56finlayup.PNG

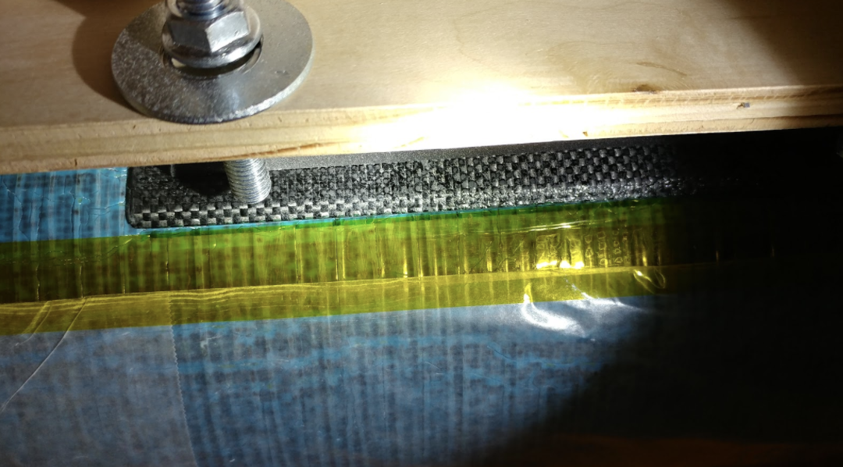
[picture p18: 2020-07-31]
doc/img/23finlayup.PNG

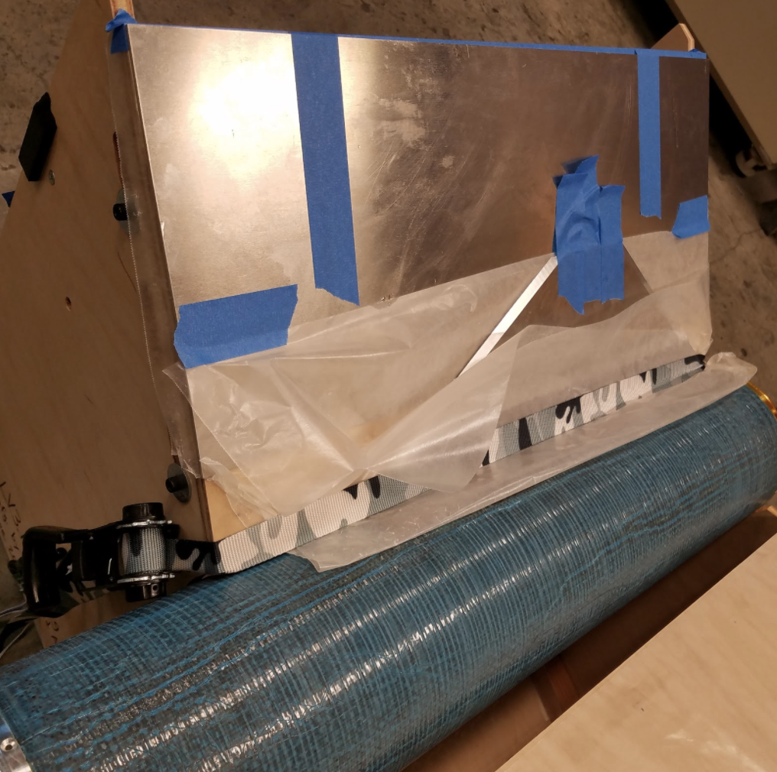
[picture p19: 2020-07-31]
doc/img/61afinlayup.PNG

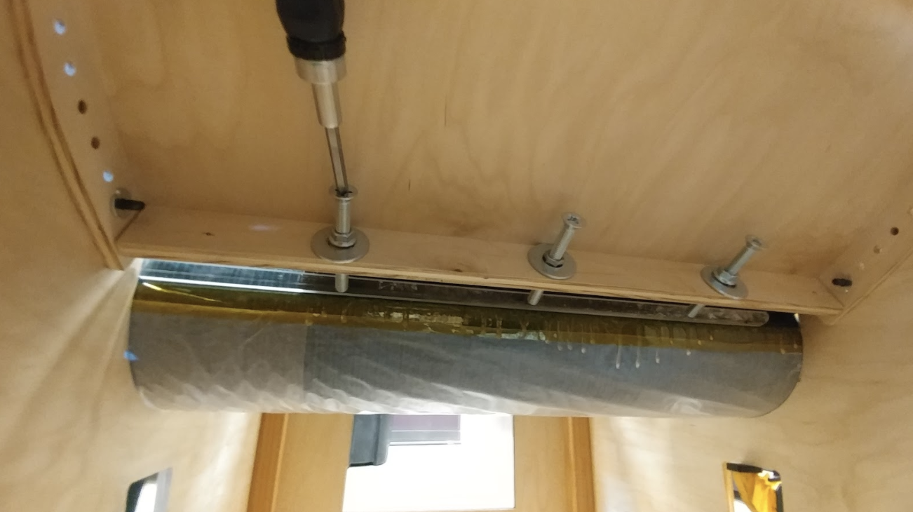
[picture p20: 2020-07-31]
doc/img/28finlayup.PNG

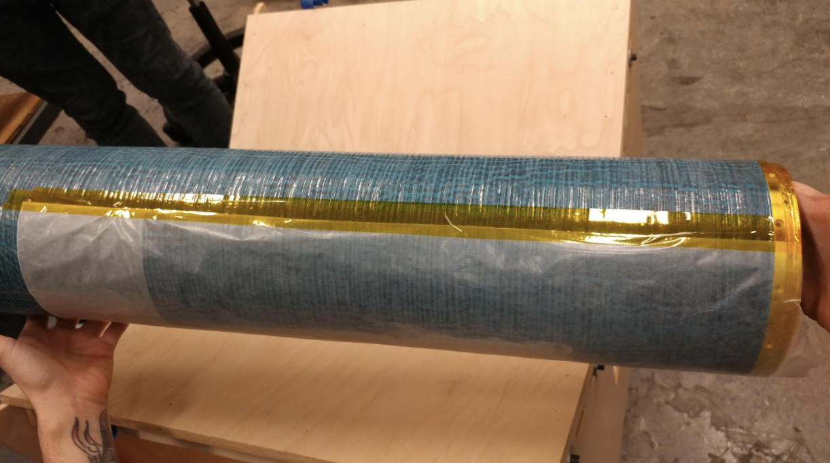
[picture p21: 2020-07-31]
doc/img/20finlayup.PNG

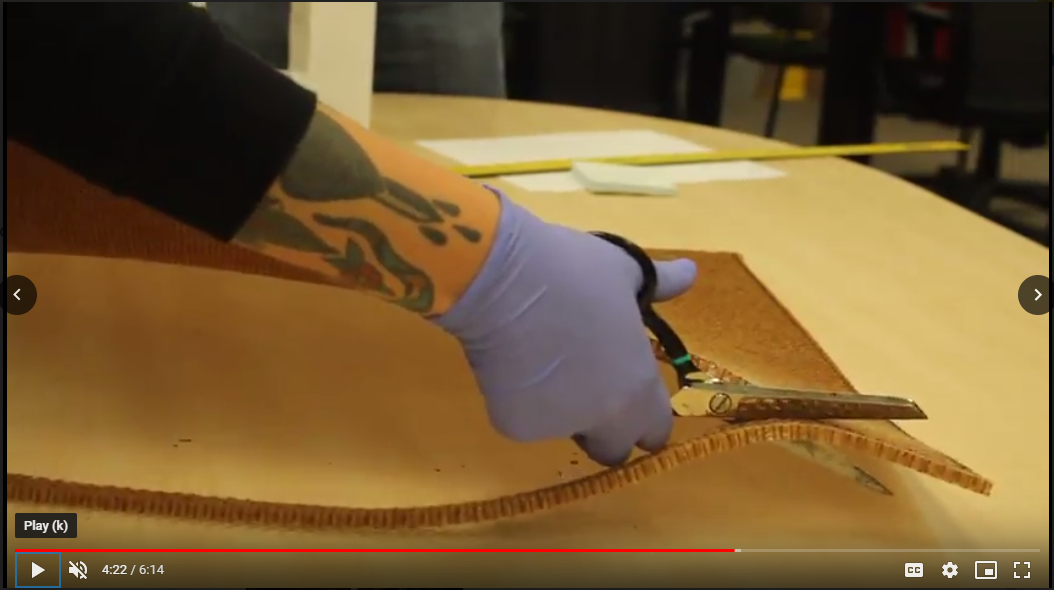
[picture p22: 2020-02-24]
doc/img/NomexTrim.PNG

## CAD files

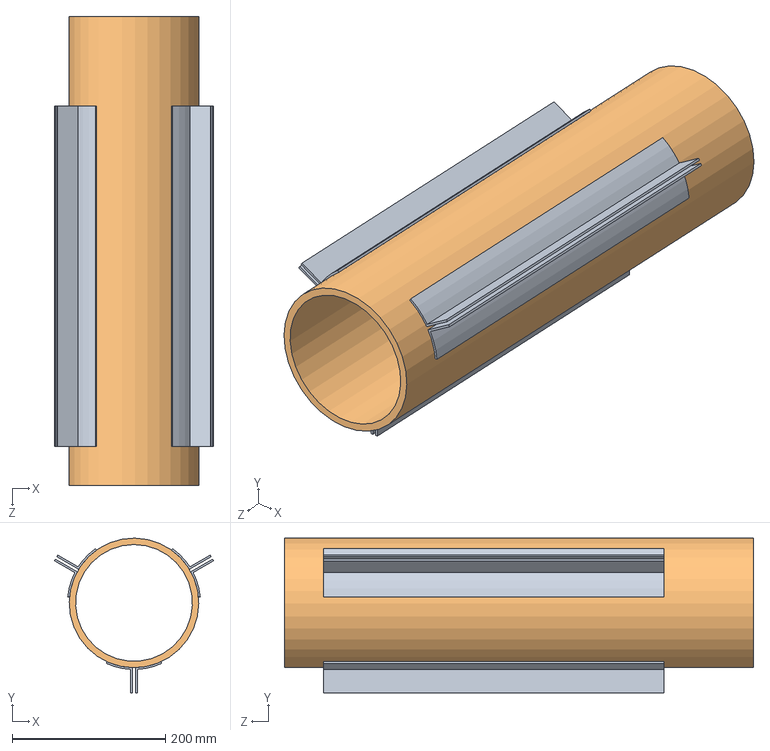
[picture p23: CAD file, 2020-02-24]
cad/finCan/Fin Can Layup Rig/Parts and Assemblies/Fin Can.SLDASM
207.7 x 202.0 x 612.1 mm
Fin Brackets
Fin Module

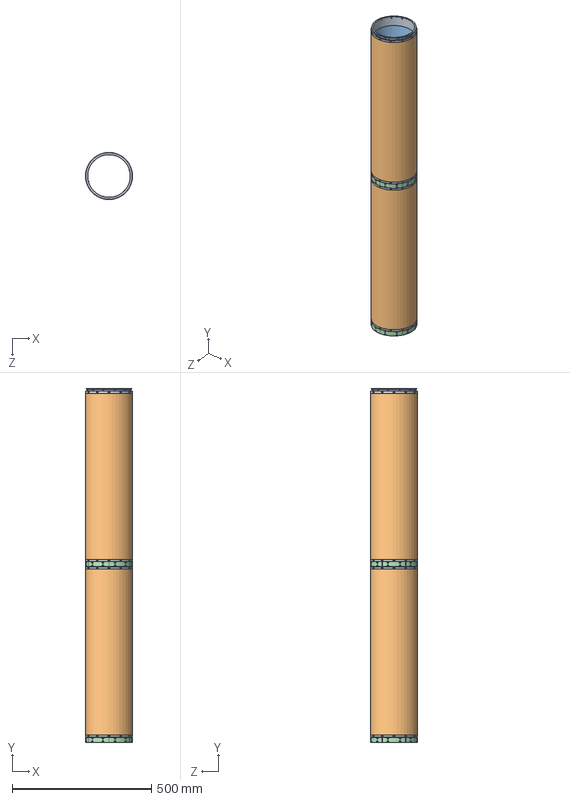
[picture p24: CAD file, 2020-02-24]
cad/modules/couplingExample.SLDASM
168.9 x 1268.9 x 168.9 mm
moduleRing x 4
compositeOuterSleeve x 2
compositeInnerSleeve x 2
clampArc x 12
4-40x0.3125_82degCSK_flatHex_91253A107_ALLOY STEEL FLAT-HEAD SOCKET CAP SCREW x 31
4-40x0.375_82degCSK_flatHex_91253A108_ALLOY STEEL FLAT-HEAD SOCKET CAP SCREW x 6

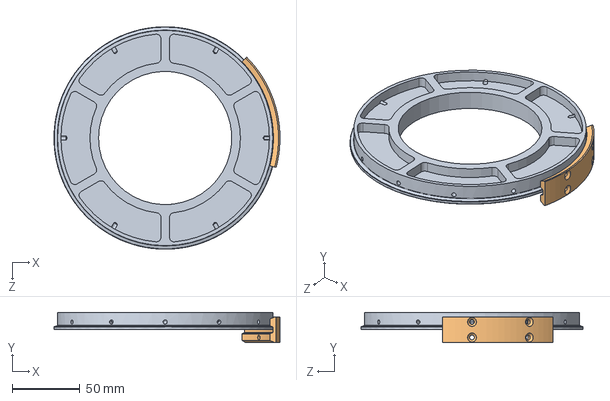
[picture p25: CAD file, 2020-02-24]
cad/thrustFlange/FlangeAndArcAssem.SLDASM
166.2 x 22.1 x 163.7 mm
thrustFlange
clampArc

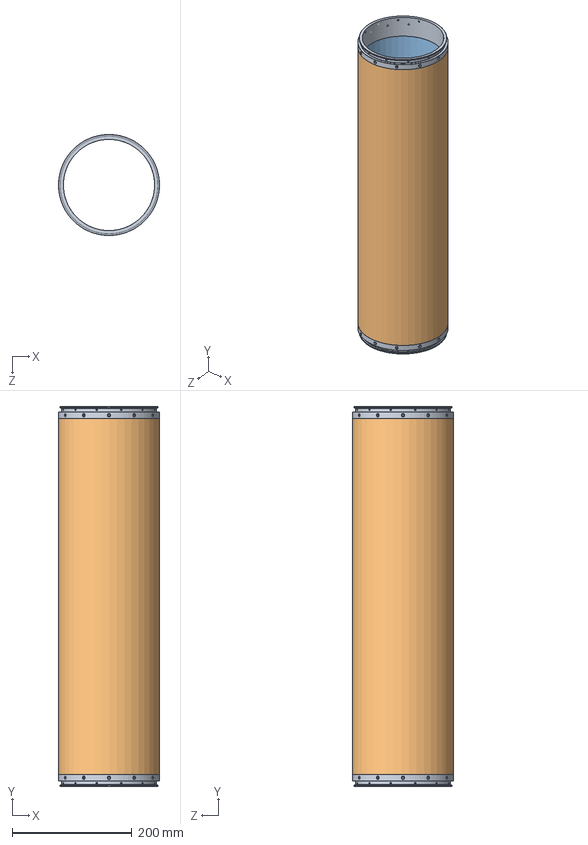
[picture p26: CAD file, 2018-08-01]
cad/modules/module24.SLDASM
168.9 x 635.1 x 168.9 mm
moduleRing x 2
compositeOuterSleeve
compositeInnerSleeve

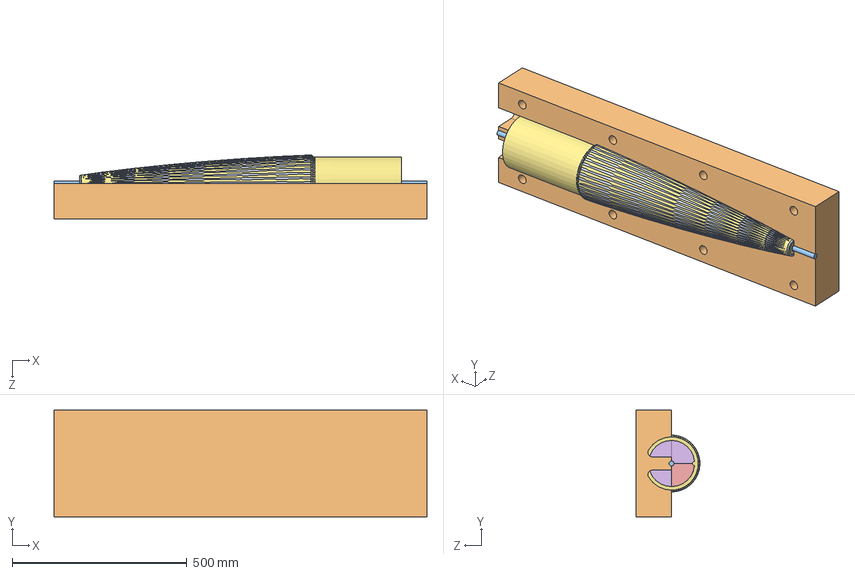
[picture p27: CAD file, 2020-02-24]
cad/nose/HalfMoldAssembly.SLDASM
1066.8 x 304.8 x 182.9 mm
Georges_Experimental_Nosecone_Half_Mold
SiliconeVolume
MandrelHalfPlug^HalfMoldAssembly

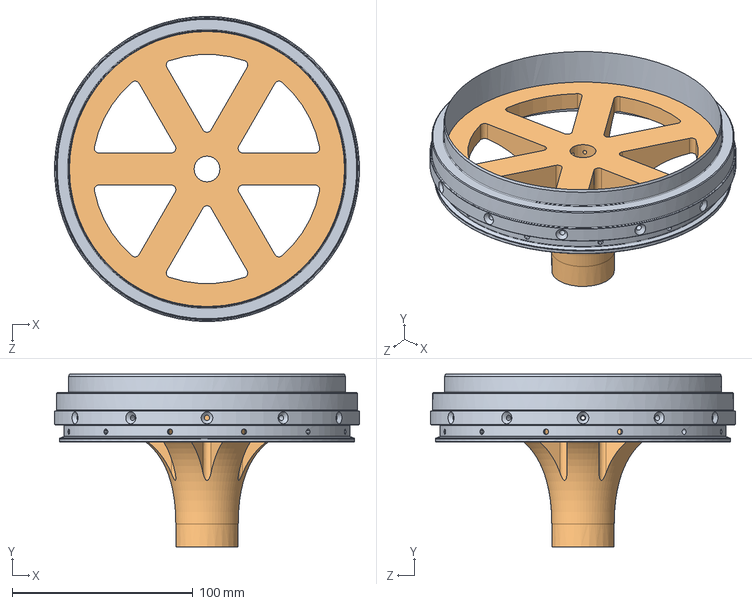
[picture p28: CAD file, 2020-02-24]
cad/nose/NostrilSpider.SLDASM
168.9 x 95.6 x 168.9 mm
moduleRing
NostrilSpider

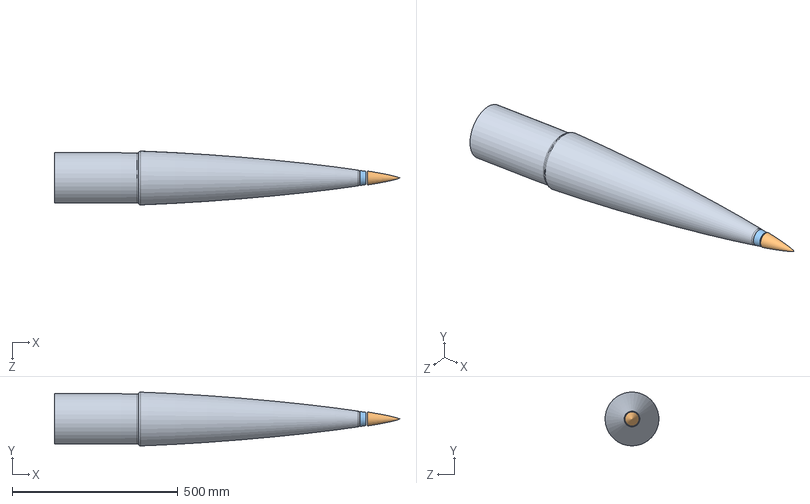
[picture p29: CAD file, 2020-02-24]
cad/nose/NoseConeAssembly.SLDASM
1041.4 x 162.5 x 162.6 mm
SiliconeVolume
Part2^NoseConeAssembly
DNUT^NoseConeAssembly

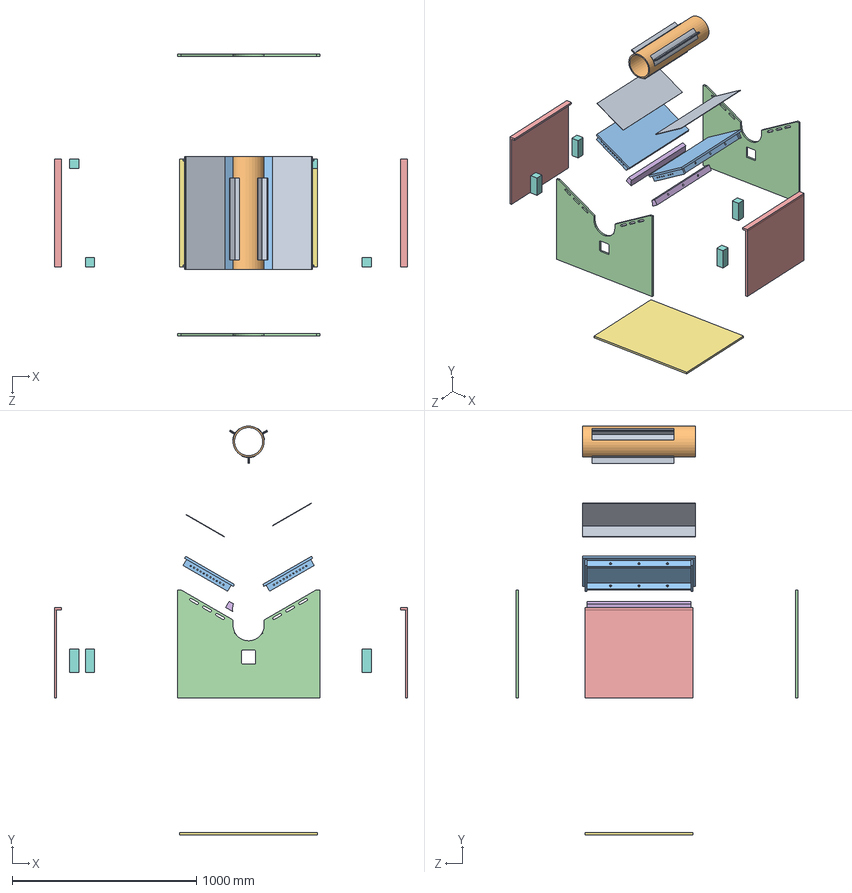
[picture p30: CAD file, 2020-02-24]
cad/finCan/Fin Can Layup Rig/Parts and Assemblies/Tip To Tip Jig.SLDASM
1915.0 x 2217.4 x 1527.0 mm
Fin Brackets
Fin Module
Bracket Alignment Surfaces^Tip To Tip Jig
Fin Can Holder Front-Back^Tip To Tip Jig x 2
Fin Can Holder Side^Tip To Tip Jig x 2
Bracket Press^Tip To Tip Jig x 2
Frame Bottom^Tip To Tip Jig
Twist Prevention Block x 4
Fin Support^Tip To Tip Jig x 2

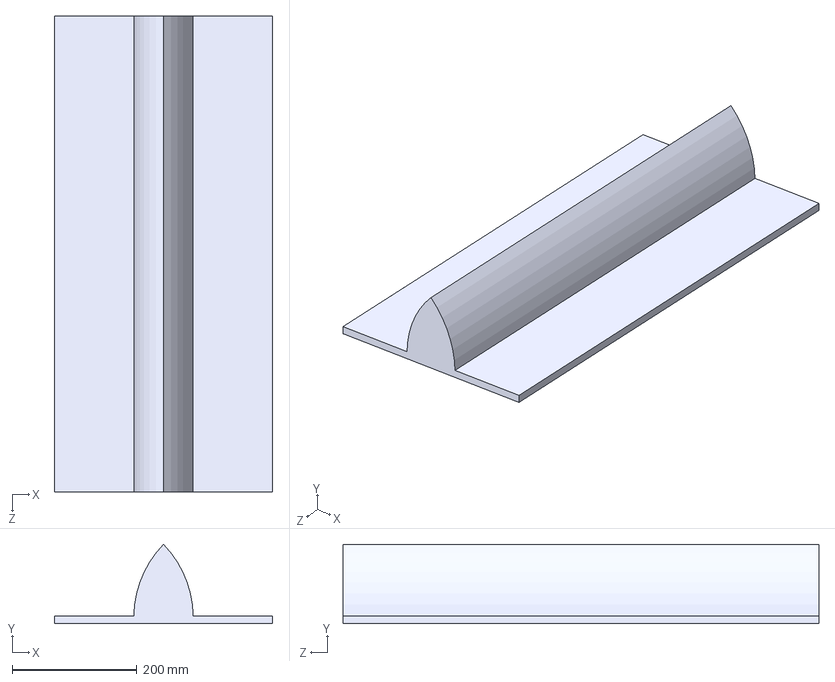
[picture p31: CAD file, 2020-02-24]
cad/Airframe Bracket Jig Machined Aluminum.STEP
349.3 x 127.2 x 762.0 mm

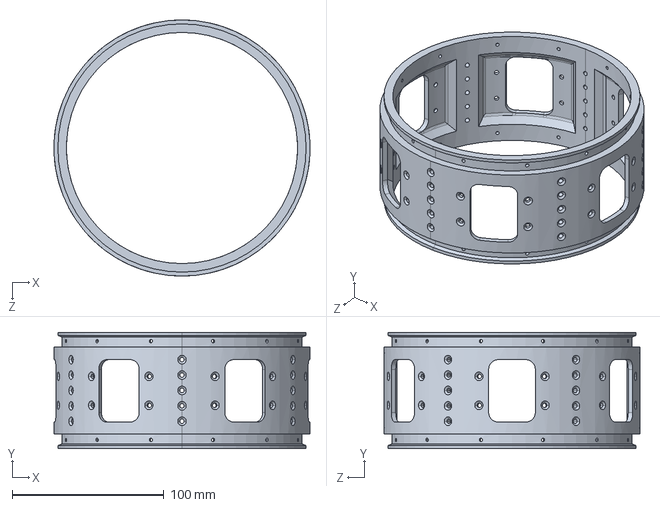
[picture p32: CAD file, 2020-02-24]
cad/build/passthroughRing1.STEP
168.8 x 76.7 x 168.9 mm

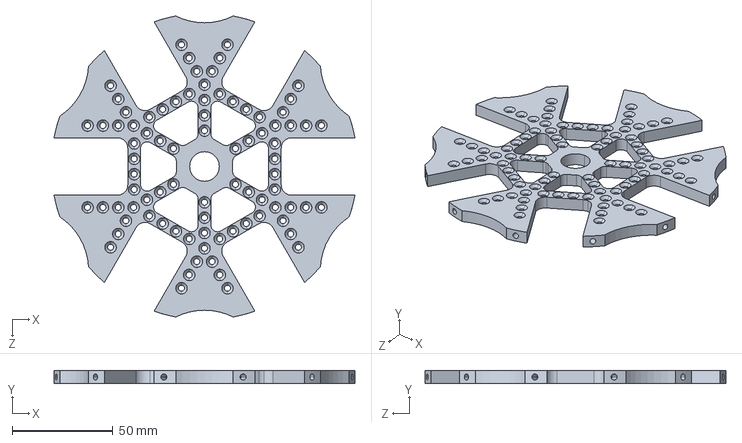
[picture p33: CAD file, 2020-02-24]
cad/bulkheads/LV3.1.7_bulkhead.STEP
149.5 x 6.35 x 149.5 mm

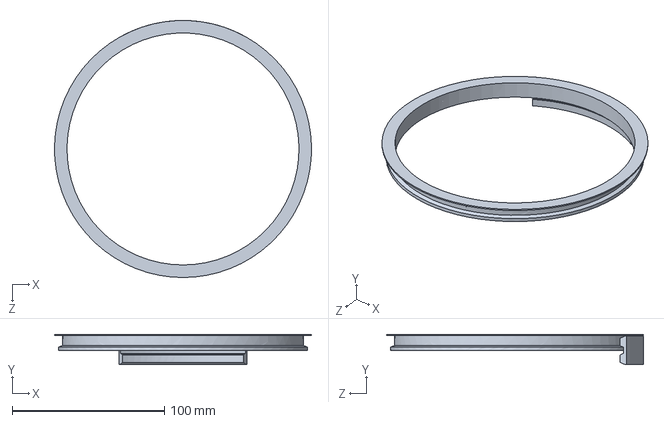
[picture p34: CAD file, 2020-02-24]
cad/coupling/couplingDefinition.SLDPRT
168.9 x 19.9 x 168.9 mm

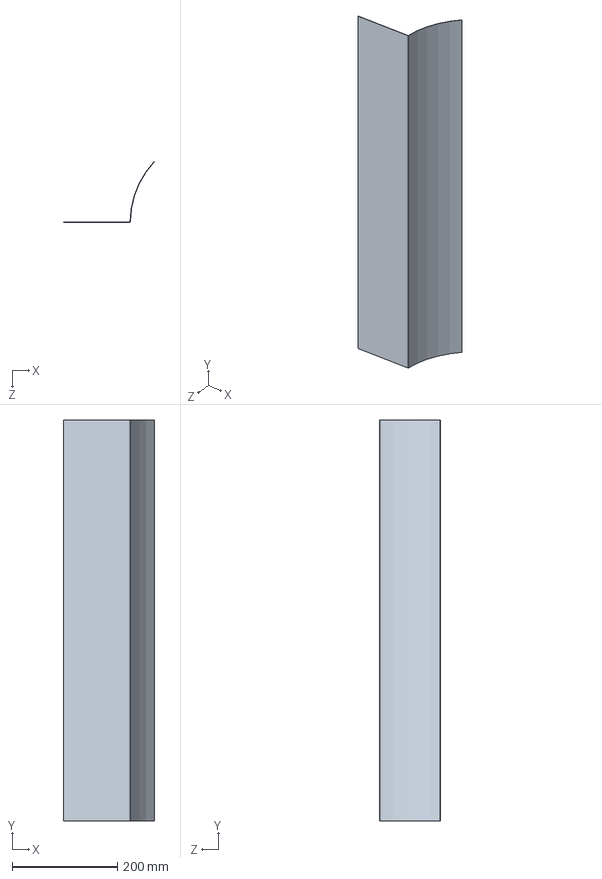
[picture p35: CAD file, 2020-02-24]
cad/finCan/Fin Can Bracket Layup Jig/Airframe Bracket Jig Sheet Metal.SLDPRT
172.5 x 762.0 x 115.9 mm

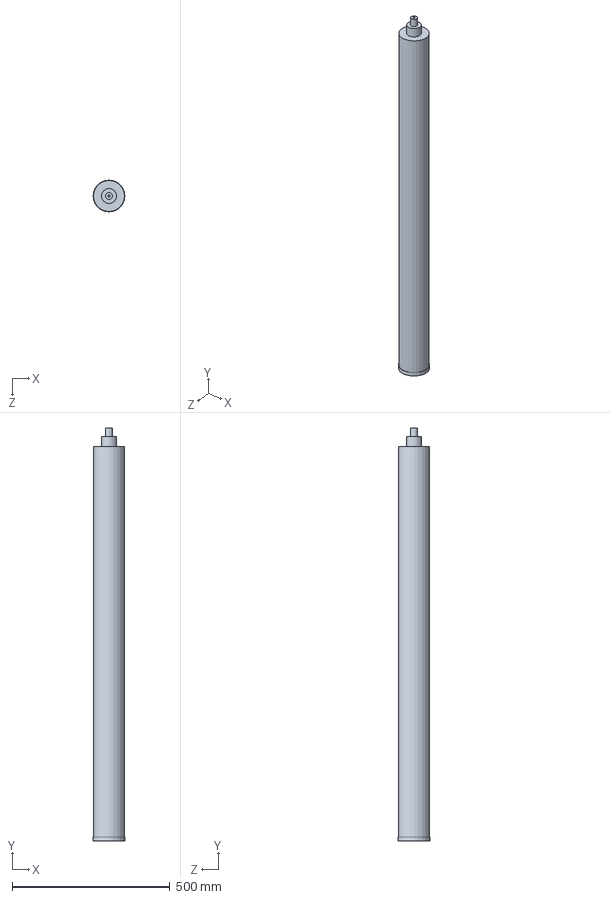
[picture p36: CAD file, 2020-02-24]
cad/finCan/motor_Cesaroni.SLDPRT
100.9 x 1310.2 x 100.9 mm

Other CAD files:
cad/fins/fin.STEP
cad/Layup_Templates/T-B-OC.SLDPRT
cad/nose/von_karmon_nose_tip2.SLDPRT
cad/passthrough/passthroughRing1.SLDPRT
cad/COTS/4-40x0.3125_82degCSK_flatHex_91253A107_ALLOY STEEL FLAT-HEAD SOCKET CAP SCREW.SLDPRT
cad/COTS/4-40x0.375_82degCSK_flatHex_91253A108_ALLOY STEEL FLAT-HEAD SOCKET CAP SCREW.SLDPRT
cad/COTS/M3x0.5x8_CSK_torxPlus_94414A713_ALLOY STEEL TORX FLAT HEAD SCREWS.SLDPRT
cad/COTS/M4x0.7x8_CSK_hex_91294A188_BLACK ALLOY STEEL FLAT-HEAD SOCKET CAP SCREW.SLDPRT
cad/COTS/quickReleaseHoseClamp_5215K130_WORK-LOAD RATED QUICK-RELEASE DUCT HOSE CLAMP.SLDPRT
cad/Layup_Templates/T-B-IC.SLDPRT
cad/Layup_Templates/T-B-NO.SLDPRT
cad/Layup_Templates/T-C-IC.SLDPRT
cad/Layup_Templates/T-C-NO.SLDPRT
cad/Layup_Templates/T-C-OC.SLDPRT
cad/build/LV3.1.7_bulkhead.STEP
cad/build/RailMountArc1u.STEP
cad/build/clampArc.STEP
cad/build/fin.STEP
cad/build/thrustFlange.STEP
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

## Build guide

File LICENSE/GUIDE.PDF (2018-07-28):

# Guide to the CERN OHL v.1.2

This document contains guidelines on how to apply the CERN OHL v.1.2 to a given hardware design, and on the use of hardware designs licensed under the CERN OHL v.1.2.

How to apply the CERN OHL v.1.2 to a hardware design Pre-requisite:

Authorship/ownership of the design must be clear and undisputed. Only the legal owner of the rights in the hardware design may decide under what conditions to make it available. If ownership is vested in more than one person/entity, there must be an agreement among the owners to release the hardware design as open hardware, and under the CERN OHL in particular.

The hardware design documentation and files package

Pack all your hardware design documentation files (schematics, layout...) as well as the documents listed below in an archive file. This will ensure the licensee downloads everything in one go. It is best to archive the files using a format everybody can open. Schematics and layouts should be included in both source form and a format readable by everybody, such as pdf.

The following documents must be distributed together with the hardware design documentation:

- Document containing the CERN OHL v.1.2 (e.g. LICENSE.PDF)
- This Guide
- Text files (plain ASCII file), where information can be added to but not removed from, listing:
- Contact point wishing to receive information about manufactured Products (see section 4.2) (e.g. PRODUCT.TXT);
- Modifications made by Licensee (see section 3.4.b) (e.g. CHANGES.TXT)

What to do with the hardware design documentation

Include in the hardware design documentation, for instance as a header, the following elements (see section 3.1 CERN OHL v.1.2):
- a copyright notice reflecting actual ownership;
- a notice that the hardware design documentation is licensed under the CERN OHL v.1.2, possibly with a link to http://ohwr.org/cernohl where the licence texts are hosted:
- “Licensed under CERN OHL v.1.2 or later”
- “Licensed under CERN OHL v.1.2”;
- a disclaimer of warranties;
- a Documentation Location if you wish to specify one;

The following is an example of header if CERN is the Licensor:

Copyright CERN 2013.

This documentation describes Open Hardware and is licensed under the CERN OHL v. 1.2.

You may redistribute and modify this documentation under the terms of the CERN OHL v.1.2. (http://ohwr.org/cernohl). This documentation is distributed WITHOUT ANY EXPRESS OR IMPLIED WARRANTY, INCLUDING OF MERCHANTABILITY, SATISFACTORY QUALITY AND FITNESS FOR A PARTICULAR PURPOSE. Please see the CERN OHL v.1.2 for applicable conditions

Include in a part of the Documentation corresponding to a visible part of the Product (e.g. silkscreen or top copper for a Printed Circuit Board):

- the licence notice: “Licensed under CERN OHL v.1.2”
- Do not include the CERN logo or the copyright notice
- the Documentation Location if you wish it to appear on the Product, thus enabling all subsequent recipients of the Products to find the Documentation.

How to deal with hardware designs licensed under the CERN OHL v.1.2
Generally speaking, you must always comply with any obligations applying to a particular design (detailed in a contract or accompanying licence). If you receive hardware designs licensed under the CERN OHL v.1.2, the obligations are to:
- Keep intact all the copyright and trademark notices and Documentation Location notices that are on the hardware design documentation;
- Keep intact the references to the CERN OHL v.1.2;
- Keep intact the disclaimer of warranties.

If you modify hardware design that you received from someone else that is licensed under the CERN OHL v.1.2, you must

- Keep intact all the notices referred to above;
- Include notices that you have modified the hardware designs, detailing what modifications where made (e.g. in a CHANGES.TXT file);
- Add the appropriate copyright notice and Documentation Location to the modifications that were made;
- license the modifications under the CERN OHL v.1.2 if you distribute them.

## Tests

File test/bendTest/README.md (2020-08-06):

# Bend Test
This directory contains info about the bend test done on 2018-12-17.

## The Data
The original video and instrumentation data can be found at [this Google Drive link](https://drive.google.com/drive/folders/1316Z5aGJLGGdGO3YifeCQpyrdhxJAECB).

`Gen2Module StressTest1.txt` contains CSV data of the instrumentaiton.
The columns are a little confusingly labelled. 
They *do not* express raw voltages!
- The first column, named "Row", simply contains the row number.
- The second column, named "Time", contains the time (%H:%M:%S %Z).
- The thrid column, named "Voltage_0(Voltage)", contains the center load in kN.
- The fourth column, named "Voltage_1(Voltage)", contains the strain in the "red"/"right" strain gauge 
  and is correctly scaled but not correctly zeroed.
- The fifth column, named "Voltage_2(Voltage)", contains the displacement of the laser extensometer markers.
  Note that the extensometer strayed away from these markers during the test, which is why there are so many jumps in the data.
- The sixth column, named "Voltage_3(Voltage)", contains the strain in the "blue"/"left" strain gauge 
  and is correctly scaled but not correctly zeroed.

## Supplemental Reading
These documents provide some relevant information.

[__Rocket airframe concepts__ by Rick Newlands](http://www.aspirespace.org.uk/downloads/Rocket%20airframe%20concepts.pdf)
covers some introductory intuition-level stuff regarding structures.

[__Aircraft Structures for Engineering Students__ by T.H.G. Megson](https://books.google.com/books/about/Aircraft_Structures_for_Engineering_Stud.html?id=z39Y6CGu7OsC)
is a general textbook on aircraft enginering, which *may* fill in the theory details that Flannigan glosses over.

### Chris Flannigan
Flannigan's work very convincingly *asserts that* his software for modal analysis works, 
but he's a little opaque on the theory and doesn't readily provide the source or even a binary.
- [__Aeroelastic Analysis of Super-Roc Vehicles__ by Chris Flanigan](https://sites.google.com/site/chrisflaniganrocketry/Home/research-and-development/Super-Roc_Simulation.pdf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)
- [__AVOIDING THE BENDS! Why Super-Roc Models Buckle and How to Design for a Successful Flight__ by Chris Flanigan (NAR 17540L1)](https://www.nar.org/wp-content/uploads/2014/08/Avoiding_the_Bends.pdf)
- [__Improved Designs for the D Super-Roc Altitude Contest__ by Chris Flanigan](https://www.apogeerockets.com/education/downloads/Newsletter353.pdf)

[Flannigan's website](https://sites.google.com/site/chrisflaniganrocketry/Home/research-and-development)
also has lots of related information.

## Point Tracking
Joe and Georges used different approaches for point tracking. 
Joe used ImageJ, while Georges used [Tracker](https://physlets.org/tracker/).
[__Manual Tracking__ by Fabrice P. Cordelières](https://imagej.nih.gov/ij/plugins/track/Manual%20Tracking%20plugin.pdf)
serves as a handbook for how to do manual point tracking with ImageJ.

The following `ffmpeg` command can be used to reformat the original videos into a format that ImageJ likes:

```
ffmpeg -i input.mp4 -an -r 1 -pix_fmt nv12 -f avi -vcodec rawvideo output.avi
```

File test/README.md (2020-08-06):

# test/
This directory is for test data and analyses. 
If you measured something or refined some "take away" information based on a measurement, it goes here.

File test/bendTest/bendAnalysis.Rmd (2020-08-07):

---
title: Analysis of LV3.1 Bend Test
author: Joe Shields
output:
    pdf_document
---

Let's take an initial look at the raw instrumentation data.

```{r loadInstrumentData, echo=F, results=F}
# read in data
indat <- read.csv('Gen2Module StressTest1.txt', skip=5) # instrumentation data
names(indat) <- c('Row', 'Time', 'Load_kN', 'strain_red', 'strain_laser', 'strain_blue')
options(digits.secs=3) # print times to ms precision

# massage the time into something manageable (decimal seconds)
indat$Time <- strptime(indat$Time, format='%H:%M:%OS %p') # see `?strptime`
seconds <- as.double(format.POSIXlt(indat$Time, "%OS"))
minutes <- as.double(format.POSIXlt(indat$Time, "%M"))
hours   <- as.double(format.POSIXlt(indat$Time, "%H"))
indat$Time <- seconds + 60*minutes + 3600*hours
indat$Time <- indat$Time - indat$Time[1] # start the clock at zero

# remove offsets
zeroingEndTime <- 100 # s, time at which to stop zeroing the system
zeroingEndInd <- which.max(indat$Time >= zeroingEndTime) # first index where this is true

loadOffset         <- mean(indat$Load_kN[1:zeroingEndInd])
strainOffset_right <- mean(indat$strain_red[1:zeroingEndInd])
strainOffset_left  <- mean(indat$strain_blue[1:zeroingEndInd])
extentOffset       <- mean(indat$strain_laser[1:zeroingEndInd])

indat$strain_red   <- indat$strain_red - strainOffset_right
indat$strain_blue  <- indat$strain_blue - strainOffset_left
indat$strain_laser <- indat$strain_laser - extentOffset

sprintf('load offset: %0.3f kN', loadOffset)
sprintf('strain offset (right): %0.3f', strainOffset_right)
sprintf('strain offset (left): %0.3f', strainOffset_left)
sprintf('extent offset: %0.3f', extentOffset)
```

```{r loadHist, echo=T}
plot(
     indat$Time, indat$Load_kN, type='l', 
     xlab='time (s)', ylab='load (kN)',
     main='Center Load History'
)
abline(v=zeroingEndTime, col='blue')
range(indat$Load_kN) # max and min loads
```

```{r strainHist_right}
plot(
     indat$Time, indat$strain_red, type='l', 
     xlab='time (s)', ylab='strain',
     main='Strain History\nRight Cell'
)
```

```{r strainHist_left}
plot(
     indat$Time, indat$strain_blue, type="l", 
     xlab='time (s)', ylab='left cell strain',
     main='Strain History', sub='Left Cell'
)
```

```{r extentHist}
plot(
     indat$Time, indat$strain_laser, type='l', 
     xlab='time (s)', ylab='center extension (in)',
     main='Extension History'
)
```

```{r blarg, eval=F}
1145*(60.0625^3)*(6+6.65)/(24*(6^3+2*6.65^3))/(4.216e6)
#right_b1 <- read.csv('tracking/block1/')
right_b2 <- read.csv('tracking/block2/right/rightSideCombined2.csv')
#right_b3 <- read.csv('tracking/block3/')
left_b1 <- read.csv('tracking/block1/leftSideCombined1.csv')
left_b2 <- read.csv('tracking/block2/left/leftSideCombined2.csv')
left_b3 <- read.csv('tracking/block3/leftSideCombined3.csv')
names(left_b1)
names(left_b2)
names(left_b3)
intersect(names(left_b1), names(left_b2))
leftDat <- merge(left_b1, left_b2)
```

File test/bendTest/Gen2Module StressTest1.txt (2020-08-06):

NI VI Logger                            
Created: 12/17/2018 6:49:40.161 PM Pacific Standard Time
Number of scans: 3148
Scan rate: 0.5 seconds

Row,Time,Voltage_0(Voltage),Voltage_1(Voltage),Voltage_2(Voltage),Voltage_3(Voltage)
1,6:23:16.171 PM,0.00193,10.4571,0.519533,15.4271
2,6:23:16.671 PM,-0.000612312,10.0504,0.522077,15.0203
3,6:23:17.171 PM,-0.000612312,10.8639,0.519533,16.2407
4,6:23:17.671 PM,0.00193,10.4571,0.522077,15.8339
5,6:23:18.171 PM,0.00193,10.8639,0.522077,15.4271
6,6:23:18.671 PM,0.00193,10.8639,0.519533,15.8339
7,6:23:19.171 PM,0.00193,10.8639,0.522077,15.8339
8,6:23:19.671 PM,0.00193,10.8639,0.522077,15.8339
9,6:23:20.171 PM,-0.000612312,10.4571,0.51699,15.8339
10,6:23:20.671 PM,0.00193,10.8639,0.522077,16.2407
11,6:23:21.171 PM,0.00193,10.4571,0.519533,15.4271
12,6:23:21.671 PM,-0.000612312,10.8639,0.519533,14.6135
13,6:23:22.171 PM,0.00193,10.8639,0.51699,15.0203
14,6:23:22.671 PM,0.00193,10.8639,0.522077,15.4271
15,6:23:23.171 PM,0.00193,10.8639,0.519533,15.4271
16,6:23:23.671 PM,-0.000612312,10.4571,0.522077,15.8339
17,6:23:24.171 PM,-0.000612312,10.4571,0.522077,15.4271
18,6:23:24.671 PM,0.00193,11.2706,0.522077,15.8339
19,6:23:25.171 PM,-0.000612312,10.4571,0.522077,15.4271
20,6:23:25.671 PM,-0.000612312,10.4571,0.519533,15.8339
21,6:23:26.171 PM,0.00193,10.8639,0.522077,15.8339
22,6:23:26.671 PM,-0.000612312,10.4571,0.522077,15.4271
23,6:23:27.171 PM,-0.000612312,10.8639,0.519533,14.6135
24,6:23:27.671 PM,0.00193,10.8639,0.522077,14.6135
25,6:23:28.171 PM,-0.000612312,10.8639,0.519533,15.8339
26,6:23:28.671 PM,-0.000612312,11.2706,0.519533,15.0203
27,6:23:29.171 PM,-0.000612312,11.6774,0.522077,15.4271
28,6:23:29.671 PM,-0.000612312,10.8639,0.522077,15.4271
29,6:23:30.171 PM,-0.000612312,11.2706,0.51699,15.8339
30,6:23:30.671 PM,-0.000612312,10.4571,0.522077,15.8339
31,6:23:31.171 PM,-0.000612312,10.8639,0.522077,14.6135
32,6:23:31.671 PM,0.00193,11.2706,0.52462,15.8339
33,6:23:32.171 PM,0.00193,10.8639,0.522077,15.8339
34,6:23:32.671 PM,0.00193,10.4571,0.519533,15.4271
35,6:23:33.171 PM,-0.000612312,10.8639,0.519533,15.8339
36,6:23:33.671 PM,-0.000612312,10.8639,0.522077,15.4271
37,6:23:34.171 PM,0.00193,10.4571,0.522077,15.4271
38,6:23:34.671 PM,-0.000612312,10.8639,0.519533,15.4271
39,6:23:35.171 PM,0.00193,11.2706,0.519533,15.8339
40,6:23:35.671 PM,0.00193,10.8639,0.522077,15.4271
41,6:23:36.171 PM,-0.000612312,10.0504,0.522077,15.8339
42,6:23:36.671 PM,0.00193,11.2706,0.519533,15.8339
43,6:23:37.171 PM,0.00193,10.8639,0.522077,15.4271
44,6:23:37.671 PM,-0.000612312,10.4571,-0.00182646,15.8339
45,6:23:38.171 PM,-0.000612312,10.8639,0.00071676,14.6135
46,6:23:38.671 PM,-0.000612312,10.4571,0.00071676,15.4271
47,6:23:39.171 PM,-0.000612312,10.8639,0.00071676,15.8339
48,6:23:39.671 PM,0.00193,10.8639,0.00071676,15.4271
49,6:23:40.171 PM,-0.000612312,10.8639,-0.00182646,15.8339
50,6:23:40.671 PM,-0.000612312,10.8639,0.00325998,15.4271
51,6:23:41.171 PM,-0.000612312,10.8639,0.00325998,16.2407
52,6:23:41.671 PM,0.00447231,10.8639,-0.00182646,15.8339
53,6:23:42.171 PM,0.00193,10.8639,0.00325998,15.0203
54,6:23:42.671 PM,0.00193,11.2706,0.00071676,15.4271
55,6:23:43.171 PM,-0.000612312,10.8639,0.00071676,15.4271
56,6:23:43.671 PM,-0.000612312,11.2706,0.00325998,16.2407
57,6:23:44.171 PM,-0.000612312,11.6774,0.00071676,15.4271
58,6:23:44.671 PM,0.00447231,10.0504,0.00071676,15.4271
59,6:23:45.171 PM,0.00193,10.4571,0.00071676,15.8339
60,6:23:45.671 PM,0.00193,10.4571,0.00325998,15.8339
61,6:23:46.171 PM,-0.00315462,11.2706,0.00071676,15.8339
62,6:23:46.671 PM,-0.00315462,10.4571,0.00325998,15.4271
63,6:23:47.171 PM,0.00193,10.4571,0.00325998,15.8339
64,6:23:47.671 PM,0.00193,10.8639,0.00325998,16.2407
65,6:23:48.171 PM,-0.00315462,10.8639,0.00071676,15.4271
66,6:23:48.671 PM,0.00193,10.4571,0.00071676,15.8339
67,6:23:49.171 PM,0.00193,10.8639,0.00071676,15.8339
68,6:23:49.671 PM,-0.00315462,10.8639,0.00071676,15.4271
69,6:23:50.171 PM,-0.000612312,10.4571,-0.00182646,15.4271
70,6:23:50.671 PM,-0.000612312,10.4571,0.00071676,15.4271
71,6:23:51.171 PM,0.00193,10.4571,0.00325998,15.8339
72,6:23:51.671 PM,0.00193,10.8639,-0.00182646,15.4271
73,6:23:52.171 PM,-0.000612312,10.4571,0.00071676,15.8339
74,6:23:52.671 PM,-0.00569693,10.4571,0.00071676,15.4271
75,6:23:53.171 PM,-0.00569693,10.4571,-0.00182646,15.4271
76,6:23:53.671 PM,-0.00315462,10.4571,-0.00182646,15.4271
77,6:23:54.171 PM,0.00193,10.4571,0.00071676,15.4271
78,6:23:54.671 PM,0.00193,11.6774,0.00071676,15.4271
79,6:23:55.171 PM,-0.000612312,10.4571,-0.00182646,15.8339
80,6:23:55.671 PM,-0.000612312,10.8639,0.00071676,15.4271
81,6:23:56.171 PM,-0.000612312,10.4571,-0.00182646,15.4271
82,6:23:56.671 PM,-0.000612312,10.4571,0.00071676,15.8339
83,6:23:57.171 PM,0.00193,10.4571,0.00325998,15.4271
84,6:23:57.671 PM,-0.000612312,10.4571,-0.00182646,15.4271
85,6:23:58.171 PM,0.00193,10.8639,0.00325998,15.8339
86,6:23:58.671 PM,-0.000612312,10.4571,0.00325998,15.8339
87,6:23:59.171 PM,-0.00569693,10.8639,0.00071676,15.4271
88,6:23:59.671 PM,-0.000612312,10.8639,0.00325998,15.4271
89,6:24:00.171 PM,0.00193,10.8639,0.00071676,15.4271
90,6:24:00.671 PM,-0.000612312,10.4571,0.00325998,15.8339
91,6:24:01.171 PM,-0.00569693,10.4571,0.00071676,15.8339
92,6:24:01.671 PM,0.00193,11.2706,0.00325998,15.4271
93,6:24:02.171 PM,-0.000612312,10.4571,0.00071676,15.4271
94,6:24:02.671 PM,0.00193,10.8639,0.00071676,15.8339
95,6:24:03.171 PM,-0.000612312,10.4571,0.00071676,15.8339
96,6:24:03.671 PM,-0.000612312,10.4571,-0.00182646,15.8339
97,6:24:04.171 PM,0.00193,11.2706,0.00325998,15.4271
98,6:24:04.671 PM,-0.000612312,11.2706,0.00071676,15.8339
99,6:24:05.171 PM,0.00447231,10.4571,0.00071676,15.4271
100,6:24:05.671 PM,-0.00315462,10.8639,-0.00182646,16.2407
101,6:24:06.171 PM,0.00193,10.8639,0.00071676,15.8339
102,6:24:06.671 PM,0.00193,11.2706,-0.00436968,15.8339
103,6:24:07.171 PM,0.00193,10.4571,0.00325998,15.8339
104,6:24:07.671 PM,0.00447231,10.4571,-0.00182646,15.8339
105,6:24:08.171 PM,-0.000612312,10.0504,0.00071676,15.4271
106,6:24:08.671 PM,0.00193,10.4571,-0.00182646,15.4271
107,6:24:09.171 PM,0.00193,10.4571,0.00071676,15.8339
108,6:24:09.671 PM,-0.00315462,10.4571,-0.00182646,16.2407
109,6:24:10.171 PM,0.00193,11.2706,-0.00182646,16.2407
110,6:24:10.671 PM,0.00193,10.4571,0.00071676,15.8339
111,6:24:11.171 PM,0.00193,11.2706,0.00071676,15.4271
112,6:24:11.671 PM,0.00193,10.4571,0.00071676,15.4271
113,6:24:12.171 PM,-0.000612312,11.2706,0.00071676,15.8339
114,6:24:12.671 PM,-0.000612312,10.4571,0.00071676,15.8339
115,6:24:13.171 PM,-0.000612312,10.8639,-0.00182646,15.0203
116,6:24:13.671 PM,-0.000612312,11.2706,0.00071676,15.8339
117,6:24:14.171 PM,0.00193,10.4571,-0.00182646,15.0203
118,6:24:14.671 PM,0.00193,10.4571,0.00325998,15.8339
119,6:24:15.171 PM,-0.000612312,10.8639,0.00325998,15.8339
120,6:24:15.671 PM,-0.000612312,10.8639,0.00071676,16.2407
121,6:24:16.171 PM,0.00193,10.4571,0.00325998,15.4271
122,6:24:16.671 PM,-0.000612312,10.0504,-0.00182646,15.8339
123,6:24:17.171 PM,-0.000612312,10.4571,0.00325998,15.4271
124,6:24:17.671 PM,-0.000612312,11.2706,0.00071676,15.8339
125,6:24:18.171 PM,0.00193,10.4571,0.00071676,15.8339
126,6:24:18.671 PM,0.00193,10.8639,0.00325998,15.4271
127,6:24:19.171 PM,0.00193,10.8639,-0.00182646,15.4271
128,6:24:19.671 PM,0.00193,10.8639,-0.00182646,15.4271
129,6:24:20.171 PM,-0.000612312,10.8639,0.00325998,15.4271
130,6:24:20.671 PM,-0.00569693,10.4571,0.00325998,15.4271
131,6:24:21.171 PM,-0.000612312,10.0504,0.0058032,15.0203
132,6:24:21.671 PM,0.00193,10.8639,0.00071676,15.4271
133,6:24:22.171 PM,0.00193,10.4571,0.00071676,16.2407
134,6:24:22.671 PM,0.00193,10.4571,-0.00182646,15.8339
135,6:24:23.171 PM,-0.000612312,10.4571,-0.00182646,15.4271
136,6:24:23.671 PM,0.00193,10.8639,0.00071676,15.4271
137,6:24:24.171 PM,-0.000612312,10.8639,-0.00182646,16.2407
138,6:24:24.671 PM,-0.000612312,10.4571,0.00325998,15.4271
139,6:24:25.171 PM,0.00193,10.8639,0.00071676,15.8339
140,6:24:25.671 PM,-0.000612312,10.4571,-0.00182646,16.2407
141,6:24:26.171 PM,-0.000612312,10.0504,0.00325998,15.8339
142,6:24:26.671 PM,0.00193,10.8639,0.00325998,15.8339
143,6:24:27.171 PM,-0.000612312,10.8639,-0.00182646,15.8339
144,6:24:27.671 PM,0.00447231,11.2706,0.00071676,15.4271
145,6:24:28.171 PM,0.00193,10.4571,0.00325998,15.8339
146,6:24:28.671 PM,0.00193,10.4571,0.00071676,15.0203
147,6:24:29.171 PM,0.00193,11.6774,-0.00182646,15.8339
148,6:24:29.671 PM,0.00193,10.4571,0.00325998,15.8339
149,6:24:30.171 PM,-0.000612312,10.8639,0.00071676,15.8339
150,6:24:30.671 PM,0.00193,11.2706,0.00071676,16.2407
151,6:24:31.171 PM,0.00193,10.4571,0.00325998,15.8339
152,6:24:31.671 PM,0.00193,10.8639,-0.00182646,15.8339
153,6:24:32.171 PM,0.00193,10.4571,0.00325998,15.4271
154,6:24:32.671 PM,-0.00569693,10.8639,0.00071676,15.8339
155,6:24:33.171 PM,0.00193,10.4571,0.00071676,15.8339
156,6:24:33.671 PM,-0.000612312,10.8639,0.00071676,15.0203
157,6:24:34.171 PM,0.00193,10.8639,-0.00182646,15.8339
158,6:24:34.671 PM,-0.000612312,10.4571,0.00071676,15.4271
159,6:24:35.171 PM,-0.000612312,10.8639,0.0058032,15.8339
160,6:24:35.671 PM,-0.000612312,11.6774,0.00071676,16.2407
161,6:24:36.171 PM,0.00193,10.4571,0.00325998,15.8339
162,6:24:36.671 PM,-0.000612312,10.8639,0.00071676,15.4271
163,6:24:37.171 PM,-0.000612312,10.4571,-0.00436968,16.2407
164,6:24:37.671 PM,0.00193,10.4571,0.00325998,15.8339
165,6:24:38.171 PM,0.00447231,11.6774,0.00071676,15.8339
166,6:24:38.671 PM,0.00193,10.4571,0.00325998,15.8339
167,6:24:39.171 PM,0.00193,10.0504,0.00071676,16.2407
168,6:24:39.671 PM,-0.000612312,10.4571,0.00071676,15.8339
169,6:24:40.171 PM,-0.000612312,10.8639,-0.00182646,15.8339
170,6:24:40.671 PM,0.00701462,10.4571,-0.00182646,15.4271
171,6:24:41.171 PM,0.00193,10.8639,0.00071676,15.4271
172,6:24:41.671 PM,-0.000612312,10.4571,0.00071676,15.8339
173,6:24:42.171 PM,0.00193,10.8639,-0.00182646,15.8339
174,6:24:42.671 PM,0.00447231,10.8639,0.00071676,15.0203
175,6:24:43.171 PM,-0.000612312,10.0504,0.0058032,15.4271
176,6:24:43.671 PM,-0.000612312,10.8639,0.00071676,15.8339
177,6:24:44.171 PM,0.00193,10.8639,0.00325998,15.8339
178,6:24:44.671 PM,-0.000612312,10.4571,0.00325998,15.8339
179,6:24:45.171 PM,-0.000612312,10.8639,0.00071676,15.8339
180,6:24:45.671 PM,0.00193,10.4571,0.00071676,15.4271
181,6:24:46.171 PM,0.00193,10.4571,0.00071676,15.4271
182,6:24:46.671 PM,0.00193,10.4571,0.00071676,15.8339
183,6:24:47.171 PM,0.00447231,10.4571,0.00325998,15.4271
184,6:24:47.671 PM,-0.00315462,10.4571,0.00071676,15.8339
185,6:24:48.171 PM,0.00447231,10.4571,0.00325998,15.8339
186,6:24:48.671 PM,0.00193,10.4571,0.00071676,15.4271
187,6:24:49.171 PM,-0.000612312,10.8639,0.00071676,15.4271
188,6:24:49.671 PM,-0.000612312,11.2706,0.00071676,15.4271
189,6:24:50.171 PM,0.00193,10.4571,0.00325998,15.8339
190,6:24:50.671 PM,-0.00569693,11.2706,0.0058032,15.4271
191,6:24:51.171 PM,0.00193,10.0504,-0.00182646,16.2407
192,6:24:51.671 PM,0.00193,10.8639,0.00071676,16.2407
193,6:24:52.171 PM,0.00193,10.8639,0.00071676,15.8339
194,6:24:52.671 PM,0.00193,10.8639,0.00325998,15.0203
195,6:24:53.171 PM,-0.000612312,11.2706,0.00071676,15.8339
196,6:24:53.671 PM,-0.000612312,10.4571,-0.00182646,15.4271
197,6:24:54.171 PM,0.00193,10.8639,0.00071676,15.8339
198,6:24:54.671 PM,-0.000612312,10.4571,0.00071676,15.0203
199,6:24:55.171 PM,0.00193,11.2706,0.00071676,15.8339
200,6:24:55.671 PM,0.00193,10.8639,0.00071676,16.2407
201,6:24:56.171 PM,0.00193,10.4571,0.00325998,16.2407
202,6:24:56.671 PM,0.00193,10.8639,0.00325998,15.8339
203,6:24:57.171 PM,0.00193,11.2706,0.00071676,15.8339
204,6:24:57.671 PM,0.00193,10.4571,0.00325998,15.8339
205,6:24:58.171 PM,0.00193,10.8639,-0.00182646,15.8339
206,6:24:58.671 PM,0.00193,10.8639,-0.00182646,15.4271
207,6:24:59.171 PM,0.00447231,10.4571,0.00071676,14.6135
208,6:24:59.671 PM,0.00955693,10.8639,0.00325998,16.2407
209,6:25:00.171 PM,0.00447231,11.2706,0.00325998,15.8339
210,6:25:00.671 PM,0.00193,11.2706,0.00071676,15.8339
211,6:25:01.171 PM,0.00701462,10.4571,0.00071676,16.6475
212,6:25:01.671 PM,0.00955693,10.4571,0.00071676,15.8339
213,6:25:02.171 PM,0.00701462,10.4571,0.00325998,15.8339
214,6:25:02.671 PM,0.00701462,10.4571,0.00071676,15.8339
215,6:25:03.171 PM,0.00447231,10.8639,0.00325998,15.0203
216,6:25:03.671 PM,0.00447231,10.8639,0.00325998,16.2407
217,6:25:04.171 PM,0.00447231,10.4571,0.00071676,15.8339
218,6:25:04.671 PM,0.00701462,10.8639,0.00325998,15.0203
219,6:25:05.171 PM,0.0120992,10.4571,0.00071676,15.8339
220,6:25:05.671 PM,0.00701462,10.4571,0.00071676,15.4271
221,6:25:06.171 PM,0.0120992,10.4571,0.00071676,15.8339
222,6:25:06.671 PM,0.0120992,10.8639,-0.00182646,15.8339
223,6:25:07.171 PM,0.0146416,10.4571,0.00071676,15.4271
224,6:25:07.671 PM,0.0171839,10.0504,0.00071676,15.8339
225,6:25:08.171 PM,0.0197262,10.0504,0.00071676,15.8339
226,6:25:08.671 PM,0.0197262,10.4571,-0.00182646,16.2407
227,6:25:09.171 PM,0.0197262,10.8639,0.00325998,15.8339
228,6:25:09.671 PM,0.0222685,10.4571,0.00071676,16.2407
229,6:25:10.171 PM,0.0222685,10.8639,-0.00436968,16.6475
230,6:25:10.671 PM,0.0248108,10.4571,-0.00182646,15.8339
231,6:25:11.171 PM,0.0298954,10.4571,0.00071676,15.8339
232,6:25:11.671 PM,0.0324377,10.4571,-0.00182646,15.4271
233,6:25:12.171 PM,0.0248108,10.8639,0.00071676,16.2407
234,6:25:12.671 PM,0.0273531,10.8639,0.00071676,15.8339
235,6:25:13.171 PM,0.0248108,11.2706,0.00071676,15.8339
236,6:25:13.671 PM,0.0222685,11.2706,0.00325998,15.4271
237,6:25:14.171 PM,0.0273531,10.8639,0.00071676,15.8339
238,6:25:14.671 PM,0.0273531,10.8639,0.00071676,15.4271
239,6:25:15.171 PM,0.0248108,11.2706,0.00325998,16.2407
240,6:25:15.671 PM,0.0222685,10.8639,0.00325998,15.4271
241,6:25:16.171 PM,0.0248108,10.4571,0.00325998,16.2407
242,6:25:16.671 PM,0.0248108,10.4571,0.00325998,16.2407
243,6:25:17.171 PM,0.0248108,10.4571,0.00071676,15.8339
244,6:25:17.671 PM,0.0273531,10.0504,0.00325998,15.8339
245,6:25:18.171 PM,0.0273531,10.8639,0.00071676,16.2407
246,6:25:18.671 PM,0.0248108,11.2706,0.00071676,16.2407
247,6:25:19.171 PM,0.0197262,10.8639,0.00071676,16.2407
248,6:25:19.671 PM,0.0248108,10.8639,0.00325998,15.8339
249,6:25:20.171 PM,0.0248108,10.8639,0.00071676,16.2407
250,6:25:20.671 PM,0.0248108,10.8639,-0.00182646,16.2407
251,6:25:21.171 PM,0.0248108,10.8639,0.00071676,15.8339
252,6:25:21.671 PM,0.0248108,10.8639,0.00071676,15.8339
253,6:25:22.171 PM,0.0248108,10.0504,0.00325998,16.2407
254,6:25:22.671 PM,0.0222685,10.4571,0.00071676,15.4271
255,6:25:23.171 PM,0.0248108,10.4571,0.00325998,15.8339
256,6:25:23.671 PM,0.0273531,10.8639,0.0058032,16.2407
257,6:25:24.171 PM,0.0248108,10.4571,-0.00182646,16.2407
258,6:25:24.671 PM,0.0248108,10.4571,0.00071676,15.4271
259,6:25:25.171 PM,0.0248108,10.8639,-0.00182646,15.0203
260,6:25:25.671 PM,0.0248108,11.2706,0.00071676,16.2407
261,6:25:26.171 PM,0.0248108,10.0504,0.00071676,15.8339
262,6:25:26.671 PM,0.0248108,10.0504,0.00325998,15.8339
263,6:25:27.171 PM,0.0248108,10.4571,0.00071676,15.8339
264,6:25:27.671 PM,0.0248108,11.2706,0.00071676,15.4271
265,6:25:28.171 PM,0.0248108,10.4571,-0.00436968,15.8339
266,6:25:28.671 PM,0.0248108,11.2706,0.00071676,15.8339
267,6:25:29.171 PM,0.0248108,10.4571,0.00071676,16.2407
268,6:25:29.671 PM,0.0222685,10.8639,0.00325998,15.4271
269,6:25:30.171 PM,0.0248108,11.2706,0.00071676,15.4271
270,6:25:30.671 PM,0.0222685,10.8639,0.00325998,15.8339
271,6:25:31.171 PM,0.0248108,10.8639,0.00325998,16.2407
272,6:25:31.671 PM,0.0197262,10.4571,0.0058032,15.4271
273,6:25:32.171 PM,0.0222685,10.8639,0.00325998,15.8339
274,6:25:32.671 PM,0.0248108,10.4571,0.00071676,16.2407
275,6:25:33.171 PM,0.0222685,10.4571,0.00071676,15.8339
276,6:25:33.671 PM,0.0273531,10.4571,0.00325998,15.4271
277,6:25:34.171 PM,0.0171839,10.8639,0.00071676,15.4271
278,6:25:34.671 PM,0.0248108,10.4571,0.00071676,16.2407
279,6:25:35.171 PM,0.0197262,10.4571,0.00325998,15.4271
280,6:25:35.671 PM,0.0248108,10.0504,0.00325998,15.8339
281,6:25:36.171 PM,0.0222685,10.4571,0.00325998,15.4271
282,6:25:36.671 PM,0.0248108,10.8639,-0.00182646,15.8339
283,6:25:37.171 PM,0.0248108,10.4571,0.00325998,15.8339
284,6:25:37.671 PM,0.0248108,10.8639,0.00325998,15.8339
285,6:25:38.171 PM,0.0248108,10.4571,0.00071676,15.8339
286,6:25:38.671 PM,0.0222685,11.2706,0.00071676,15.4271
287,6:25:39.171 PM,0.0222685,10.4571,0.00325998,15.8339
288,6:25:39.671 PM,0.0248108,11.2706,0.00071676,16.2407
289,6:25:40.171 PM,0.0222685,10.8639,0.00071676,15.4271
290,6:25:40.671 PM,0.0222685,10.8639,0.00071676,15.8339
291,6:25:41.171 PM,0.0248108,10.8639,-0.00182646,15.8339
292,6:25:41.671 PM,0.0248108,11.2706,0.00325998,15.8339
293,6:25:42.171 PM,0.0248108,10.8639,-0.00182646,15.8339
294,6:25:42.671 PM,0.0248108,10.8639,0.00325998,15.4271
295,6:25:43.171 PM,0.0248108,10.4571,0.00071676,15.8339
296,6:25:43.671 PM,0.0248108,11.2706,0.00071676,15.8339
297,6:25:44.171 PM,0.0273531,10.8639,0.0058032,16.2407
298,6:25:44.671 PM,0.0298954,10.4571,-0.00182646,15.8339
299,6:25:45.171 PM,0.0273531,10.0504,0.00071676,16.2407
300,6:25:45.671 PM,0.0298954,10.0504,-0.00182646,15.8339
301,6:25:46.171 PM,0.0298954,11.2706,0.00325998,15.4271
302,6:25:46.671 PM,0.0273531,10.4571,0.00325998,15.4271
303,6:25:47.171 PM,0.0324377,10.8639,0.00071676,16.2407
304,6:25:47.671 PM,0.0273531,10.4571,0.00071676,15.8339
305,6:25:48.171 PM,0.0298954,10.4571,0.00325998,15.8339
306,6:25:48.671 PM,0.0298954,10.4571,0.00071676,15.4271
307,6:25:49.171 PM,0.0324377,10.4571,0.00071676,15.8339
308,6:25:49.671 PM,0.0298954,10.4571,0.00071676,15.8339
309,6:25:50.171 PM,0.0298954,10.8639,-0.00182646,16.2407
310,6:25:50.671 PM,0.0298954,10.4571,0.00325998,15.8339
311,6:25:51.171 PM,0.0324377,10.8639,0.00325998,15.8339
312,6:25:51.671 PM,0.0324377,10.4571,0.0058032,15.8339
313,6:25:52.171 PM,0.03498,10.4571,0.00071676,15.8339
314,6:25:52.671 PM,0.03498,10.8639,-0.00182646,15.8339
315,6:25:53.171 PM,0.0324377,10.8639,0.00325998,16.2407
316,6:25:53.671 PM,0.03498,10.8639,0.00071676,16.2407
317,6:25:54.171 PM,0.03498,10.8639,0.00071676,16.2407
318,6:25:54.671 PM,0.03498,10.0504,-0.00182646,15.8339
319,6:25:55.171 PM,0.0375224,10.4571,0.00325998,15.8339
320,6:25:55.671 PM,0.03498,10.4571,0.00071676,15.4271
321,6:25:56.171 PM,0.0375224,10.4571,0.00325998,16.2407
322,6:25:56.671 PM,0.03498,10.8639,0.00071676,15.8339
323,6:25:57.171 PM,0.03498,10.8639,0.00071676,15.8339
324,6:25:57.671 PM,0.03498,10.8639,0.00071676,15.8339
325,6:25:58.171 PM,0.0375224,10.4571,0.00071676,15.8339
326,6:25:58.671 PM,0.0375224,10.8639,-0.00182646,15.8339
327,6:25:59.171 PM,0.0400647,10.8639,0.00325998,15.4271
328,6:25:59.671 PM,0.0400647,10.4571,0.00325998,15.8339
329,6:26:00.171 PM,0.0400647,10.4571,-0.00182646,16.2407
330,6:26:00.671 PM,0.0400647,10.0504,0.0058032,15.8339
331,6:26:01.171 PM,0.0451493,10.4571,0.00071676,15.8339
332,6:26:01.671 PM,0.0375224,10.8639,0.00071676,15.8339
333,6:26:02.171 PM,0.0400647,10.8639,0.00071676,15.8339
334,6:26:02.671 PM,0.042607,11.6774,0.0058032,16.2407
335,6:26:03.171 PM,0.0400647,10.4571,0.00071676,16.2407
336,6:26:03.671 PM,0.042607,10.4571,0.0058032,16.2407
337,6:26:04.171 PM,0.0400647,10.0504,0.00071676,15.8339
338,6:26:04.671 PM,0.0400647,11.2706,0.00325998,15.8339
339,6:26:05.171 PM,0.0400647,10.0504,0.00325998,16.2407
340,6:26:05.671 PM,0.042607,10.8639,0.00071676,15.8339
341,6:26:06.171 PM,0.042607,10.4571,0.00325998,15.8339
342,6:26:06.671 PM,0.042607,11.2706,-0.00182646,17.0543
343,6:26:07.171 PM,0.042607,10.8639,0.00325998,15.8339
344,6:26:07.671 PM,0.042607,10.8639,0.00325998,15.8339
345,6:26:08.171 PM,0.042607,10.8639,0.00071676,15.8339
346,6:26:08.671 PM,0.0451493,10.8639,0.00325998,15.4271
347,6:26:09.171 PM,0.0451493,10.4571,0.00325998,15.8339
348,6:26:09.671 PM,0.042607,10.8639,0.00325998,15.8339
349,6:26:10.171 PM,0.0451493,11.2706,0.00071676,16.2407
350,6:26:10.671 PM,0.0451493,10.8639,0.00325998,15.8339
351,6:26:11.171 PM,0.0400647,10.8639,0.00325998,15.8339
352,6:26:11.671 PM,0.0451493,10.4571,0.00325998,15.8339
353,6:26:12.171 PM,0.0476916,10.8639,0.00071676,16.6475
354,6:26:12.671 PM,0.0451493,11.2706,0.00325998,16.2407
355,6:26:13.171 PM,0.0451493,10.8639,0.00325998,15.8339
356,6:26:13.671 PM,0.0451493,10.8639,0.00325998,15.4271
357,6:26:14.171 PM,0.042607,11.2706,0.00071676,15.4271
358,6:26:14.671 PM,0.0476916,10.8639,0.00325998,15.8339
359,6:26:15.171 PM,0.0451493,10.4571,0.00325998,15.8339
360,6:26:15.671 PM,0.0476916,11.2706,0.00325998,15.8339
361,6:26:16.171 PM,0.042607,10.8639,0.00325998,15.8339
362,6:26:16.671 PM,0.0476916,11.6774,0.00325998,16.2407
363,6:26:17.171 PM,0.0451493,10.4571,0.00071676,15.8339
364,6:26:17.671 PM,0.0502339,10.0504,0.00071676,15.8339
365,6:26:18.171 PM,0.0502339,10.8639,0.0058032,15.8339
366,6:26:18.671 PM,0.0451493,10.8639,0.00325998,15.8339
367,6:26:19.171 PM,0.0476916,10.0504,0.00325998,15.8339
368,6:26:19.671 PM,0.0476916,10.4571,0.00325998,15.8339
369,6:26:20.171 PM,0.0502339,10.8639,0.00071676,15.4271
370,6:26:20.671 PM,0.0527762,10.8639,0.00071676,16.2407
371,6:26:21.171 PM,0.0502339,10.8639,0.00325998,16.2407
372,6:26:21.671 PM,0.0527762,11.2706,0.00325998,15.8339
373,6:26:22.171 PM,0.0527762,10.4571,0.00325998,16.2407
374,6:26:22.671 PM,0.0527762,11.2706,0.00071676,15.4271
375,6:26:23.171 PM,0.0527762,10.8639,0.00325998,15.4271
376,6:26:23.671 PM,0.0527762,10.0504,0.00325998,15.8339
377,6:26:24.171 PM,0.0527762,10.8639,0.00325998,16.2407
378,6:26:24.671 PM,0.0527762,10.4571,0.00071676,15.8339
379,6:26:25.171 PM,0.0527762,10.4571,0.00325998,16.2407
380,6:26:25.671 PM,0.0502339,10.4571,0.00325998,16.6475
381,6:26:26.171 PM,0.0553185,10.8639,0.0058032,16.2407
382,6:26:26.671 PM,0.0553185,10.4571,0.00325998,16.2407
383,6:26:27.171 PM,0.0553185,10.4571,0.0058032,16.2407
384,6:26:27.671 PM,0.0553185,10.8639,0.0058032,15.8339
385,6:26:28.171 PM,0.0527762,10.4571,0.00325998,15.8339
386,6:26:28.671 PM,0.0553185,10.8639,0.0058032,16.2407
387,6:26:29.171 PM,0.0553185,10.8639,0.00325998,16.2407
388,6:26:29.671 PM,0.0553185,10.8639,0.00325998,16.2407
389,6:26:30.171 PM,0.0578608,10.8639,0.00325998,16.2407
390,6:26:30.671 PM,0.0527762,10.8639,0.0058032,16.2407
391,6:26:31.171 PM,0.0578608,10.4571,0.00325998,16.2407
392,6:26:31.671 PM,0.0553185,10.8639,0.00325998,15.8339
393,6:26:32.171 PM,0.0553185,11.2706,0.00071676,15.8339
394,6:26:32.671 PM,0.0604031,10.4571,0.00325998,15.8339
395,6:26:33.171 PM,0.0578608,10.4571,0.00325998,15.8339
396,6:26:33.671 PM,0.0629455,10.8639,0.00325998,16.2407
397,6:26:34.171 PM,0.0604031,10.4571,0.0058032,16.2407
398,6:26:34.671 PM,0.0604031,11.6774,0.00325998,15.8339
399,6:26:35.171 PM,0.0578608,10.4571,0.00071676,16.2407
400,6:26:35.671 PM,0.0604031,10.8639,0.00325998,15.8339
401,6:26:36.171 PM,0.0527762,10.8639,0.00325998,16.2407
402,6:26:36.671 PM,0.0604031,10.8639,0.00071676,16.2407
403,6:26:37.171 PM,0.0604031,10.0504,0.00325998,16.2407
404,6:26:37.671 PM,0.0604031,10.4571,0.00071676,16.2407
405,6:26:38.171 PM,0.0604031,10.4571,0.00071676,16.2407
406,6:26:38.671 PM,0.0604031,10.8639,0.00071676,16.2407
407,6:26:39.171 PM,0.0629455,11.6774,0.0058032,16.2407
408,6:26:39.671 PM,0.0654878,10.8639,0.0058032,16.2407
409,6:26:40.171 PM,0.0604031,11.2706,0.00325998,16.2407
410,6:26:40.671 PM,0.0604031,10.8639,0.00325998,15.8339
411,6:26:41.171 PM,0.0629455,10.4571,0.0058032,15.4271
412,6:26:41.671 PM,0.0629455,10.4571,0.00325998,16.2407
413,6:26:42.171 PM,0.0654878,10.4571,0.0058032,15.8339
414,6:26:42.671 PM,0.0604031,10.4571,0.00834642,15.8339
415,6:26:43.171 PM,0.0629455,10.8639,0.0058032,15.8339
416,6:26:43.671 PM,0.0654878,10.4571,0.00325998,16.2407
417,6:26:44.171 PM,0.0680301,10.8639,0.00071676,15.8339
418,6:26:44.671 PM,0.0654878,11.2706,0.00325998,15.8339
419,6:26:45.171 PM,0.0654878,10.4571,0.00325998,16.2407
420,6:26:45.671 PM,0.0705724,10.8639,0.0058032,16.6475
421,6:26:46.171 PM,0.0705724,11.2706,0.0058032,15.8339
422,6:26:46.671 PM,0.0731147,10.4571,0.00325998,15.8339
423,6:26:47.171 PM,0.075657,10.8639,0.0058032,16.2407
424,6:26:47.671 PM,0.075657,11.2706,0.00325998,16.2407
425,6:26:48.171 PM,0.0832839,10.4571,0.00325998,15.8339
426,6:26:48.671 PM,0.0807416,11.6774,0.00325998,16.2407
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

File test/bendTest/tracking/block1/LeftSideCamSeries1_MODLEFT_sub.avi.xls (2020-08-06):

Nr | TID | PID | x [inch] | y [inch] | t [sec] | I [val] | Len [inch] | D2S [inch] | D2R [inch] | D2P [inch] | v [inch/sec] | α [deg] | Δα [deg]
1 | 1 | 14 | 1.049 | 0.448 | 0 | 103.6 | 0 | 0 | NA | NA | NA | NA | NA
2 | 1 | 15 | 1.046 | 0.374 | 1 | 105 | 0.075 | 0.075 | NA | 0.075 | 0.075 | -91.591 | NA
3 | 1 | 16 | 1.098 | 0.448 | 2 | 107.5 | 0.166 | 0.05 | NA | 0.091 | 0.091 | 55.222 | 146.813
4 | 1 | 17 | 1.018 | 0.451 | 3 | 116.2 | 0.246 | 0.03 | NA | 0.08 | 0.08 | 178.512 | 123.29
5 | 1 | 13 | 1.031 | 0.415 | 11 | 107.4 | 0.283 | 0.038 | NA | 0.037 | 0.005 | -70.56 | 110.928
6 | 1 | 19 | 1.018 | 0.451 | 29 | 76.6 | 0.321 | 0.03 | NA | 0.037 | 0.002 | 109.44 | 180
7 | 1 | 18 | 1.018 | 0.451 | 34 | 71 | 0.321 | 0.03 | NA | 0 | 0 | 0 | -109.44
8 | 1 | 12 | 1.032 | 0.412 | 41 | 90.8 | 0.361 | 0.04 | NA | 0.041 | 0.006 | -70.641 | -70.641
9 | 1 | 11 | 1.027 | 0.414 | 75 | 89.6 | 0.367 | 0.041 | NA | 0.006 | 1.644E-4 | 158.199 | -131.16
10 | 1 | 10 | 1.031 | 0.402 | 134 | 119.9 | 0.38 | 0.05 | NA | 0.013 | 2.226E-4 | -71.565 | 130.236
11 | 1 | 9 | 1.029 | 0.401 | 188 | 106.9 | 0.382 | 0.052 | NA | 0.002 | 4.299E-5 | -153.435 | -81.87
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

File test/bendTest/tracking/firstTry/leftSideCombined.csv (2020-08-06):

Nr | TID | PID | x [inch] | y [inch] | t [sec] | I [val] | Len [inch] | D2S [inch] | D2R [inch] | D2P [inch] | v [inch/sec] | α [deg] | Δα [deg]
1 | 4 | 1 | 1.054 | 0.449 | 0 | 105.6 | 0 | 0 | NA | NA | NA | NA | NA
2 | 4 | 2 | 1.055 | 0.373 | 1 | 75 | 0.077 | 0.077 | NA | 0.077 | 0.077 | -89.226 | NA
3 | 4 | 3 | 1.108 | 0.448 | 2 | 80.3 | 0.169 | 0.054 | NA | 0.092 | 0.092 | 55.061 | 144.286
4 | 4 | 4 | 1.036 | 0.452 | 3 | 95.3 | 0.241 | 0.018 | NA | 0.072 | 0.072 | 177.51 | 122.45
5 | 4 | 5 | 1.039 | 0.415 | 4 | 77.9 | 0.277 | 0.037 | NA | 0.036 | 0.036 | -85.101 | 97.389
6 | 4 | 6 | 1.044 | 0.414 | 10 | 92.2 | 0.283 | 0.037 | NA | 0.005 | 8.822E-4 | -11.31 | 73.791
7 | 4 | 7 | 1.036 | 0.401 | 12 | 102.2 | 0.299 | 0.052 | NA | 0.016 | 0.008 | -121.608 | -110.298
8 | 4 | 8 | 1.038 | 0.414 | 16 | 74.6 | 0.312 | 0.039 | NA | 0.014 | 0.003 | 81.254 | -157.139
9 | 4 | 9 | 1.038 | 0.414 | 21 | 77.1 | 0.312 | 0.039 | NA | 0 | 0 | 0 | -81.254
10 | 4 | 10 | 1.041 | 0.414 | 66 | 74.3 | 0.315 | 0.037 | NA | 0.003 | 6.92E-5 | 0 | 0
11 | 4 | 11 | 1.039 | 0.405 | 118 | 84.8 | 0.325 | 0.047 | NA | 0.01 | 1.84E-4 | -102.529 | -102.529
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

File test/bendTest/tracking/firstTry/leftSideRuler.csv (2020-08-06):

Nr | TID | PID | x [inch] | y [inch] | t [sec] | I [val] | Len [inch] | D2S [inch] | D2R [inch] | D2P [inch] | v [inch/sec] | α [deg] | Δα [deg]
1 | 4 | 1 | 1.054 | 0.449 | 0 | 105.6 | 0 | 0 | NA | NA | NA | NA | NA
2 | 4 | 2 | 1.055 | 0.373 | 1 | 75 | 0.077 | 0.077 | NA | 0.077 | 0.077 | -89.226 | NA
3 | 4 | 3 | 1.108 | 0.448 | 2 | 80.3 | 0.169 | 0.054 | NA | 0.092 | 0.092 | 55.061 | 144.286
4 | 4 | 4 | 1.036 | 0.452 | 3 | 95.3 | 0.241 | 0.018 | NA | 0.072 | 0.072 | 177.51 | 122.45
5 | 4 | 5 | 1.039 | 0.415 | 4 | 77.9 | 0.277 | 0.037 | NA | 0.036 | 0.036 | -85.101 | 97.389
6 | 4 | 6 | 1.044 | 0.414 | 10 | 92.2 | 0.283 | 0.037 | NA | 0.005 | 8.822E-4 | -11.31 | 73.791
7 | 4 | 7 | 1.036 | 0.401 | 12 | 102.2 | 0.299 | 0.052 | NA | 0.016 | 0.008 | -121.608 | -110.298
8 | 4 | 8 | 1.038 | 0.414 | 16 | 74.6 | 0.312 | 0.039 | NA | 0.014 | 0.003 | 81.254 | -157.139
9 | 4 | 9 | 1.038 | 0.414 | 21 | 77.1 | 0.312 | 0.039 | NA | 0 | 0 | 0 | -81.254
10 | 4 | 10 | 1.041 | 0.414 | 66 | 74.3 | 0.315 | 0.037 | NA | 0.003 | 6.92E-5 | 0 | 0
11 | 4 | 11 | 1.039 | 0.405 | 118 | 84.8 | 0.325 | 0.047 | NA | 0.01 | 1.84E-4 | -102.529 | -102.529
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

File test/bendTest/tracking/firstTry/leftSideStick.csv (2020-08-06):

Nr | TID | PID | x [inch] | y [inch] | t [sec] | I [val] | Len [inch] | D2S [inch] | D2R [inch] | D2P [inch] | v [inch/sec] | α [deg] | Δα [deg]
19 | 7 | 8 | 0.704 | 4.111 | 0 | 100 | 0 | 0 | NA | NA | NA | NA | NA
20 | 7 | 9 | 0.702 | 4.032 | 1 | 90.3 | 0.079 | 0.079 | NA | 0.079 | 0.079 | -91.507 | NA
21 | 7 | 10 | 0.737 | 4.113 | 2 | 60.1 | 0.167 | 0.033 | NA | 0.088 | 0.088 | 66.448 | 157.955
22 | 7 | 11 | 0.695 | 4.113 | 3 | 126.7 | 0.209 | 0.009 | NA | 0.042 | 0.042 | 180 | 113.552
23 | 7 | 12 | 0.689 | 4.075 | 4 | 123.4 | 0.247 | 0.038 | NA | 0.038 | 0.038 | -99.462 | 80.538
24 | 7 | 13 | 0.709 | 4.064 | 13 | 152.6 | 0.269 | 0.047 | NA | 0.023 | 0.003 | -31.264 | 68.199
25 | 7 | 14 | 0.679 | 4.069 | 20 | 106.9 | 0.3 | 0.048 | NA | 0.03 | 0.004 | 169.461 | -159.275
26 | 7 | 15 | 0.673 | 4.077 | 38 | 92.9 | 0.31 | 0.046 | NA | 0.01 | 5.767E-4 | 126.87 | -42.591
27 | 7 | 16 | 0.675 | 4.08 | 51 | 117.4 | 0.314 | 0.042 | NA | 0.004 | 3.011E-4 | 45 | -81.87
28 | 7 | 17 | 0.677 | 4.075 | 72 | 99 | 0.319 | 0.044 | NA | 0.005 | 2.399E-4 | -74.055 | -119.055
29 | 7 | 18 | 0.675 | 4.071 | 91 | 86.9 | 0.324 | 0.049 | NA | 0.005 | 2.443E-4 | -116.565 | -42.51
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

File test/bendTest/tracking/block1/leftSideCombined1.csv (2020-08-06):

Nr | TID | PID | x [inch] | y [inch] | t [sec] | I [val] | Len [inch] | D2S [inch] | D2R [inch] | D2P [inch] | v [inch/sec] | α [deg] | Δα [deg]
1 | 1 | 14 | 1.049 | 0.448 | 0 | 103.6 | 0 | 0 | NA | NA | NA | NA | NA
2 | 1 | 15 | 1.046 | 0.374 | 1 | 105 | 0.075 | 0.075 | NA | 0.075 | 0.075 | -91.591 | NA
3 | 1 | 16 | 1.098 | 0.448 | 2 | 107.5 | 0.166 | 0.05 | NA | 0.091 | 0.091 | 55.222 | 146.813
4 | 1 | 17 | 1.018 | 0.451 | 3 | 116.2 | 0.246 | 0.03 | NA | 0.08 | 0.08 | 178.512 | 123.29
5 | 1 | 13 | 1.031 | 0.415 | 11 | 107.4 | 0.283 | 0.038 | NA | 0.037 | 0.005 | -70.56 | 110.928
6 | 1 | 19 | 1.018 | 0.451 | 29 | 76.6 | 0.321 | 0.03 | NA | 0.037 | 0.002 | 109.44 | 180
7 | 1 | 18 | 1.018 | 0.451 | 34 | 71 | 0.321 | 0.03 | NA | 0 | 0 | 0 | -109.44
8 | 1 | 12 | 1.032 | 0.412 | 41 | 90.8 | 0.361 | 0.04 | NA | 0.041 | 0.006 | -70.641 | -70.641
9 | 1 | 11 | 1.027 | 0.414 | 75 | 89.6 | 0.367 | 0.041 | NA | 0.006 | 1.644E-4 | 158.199 | -131.16
10 | 1 | 10 | 1.031 | 0.402 | 134 | 119.9 | 0.38 | 0.05 | NA | 0.013 | 2.226E-4 | -71.565 | 130.236
11 | 1 | 9 | 1.029 | 0.401 | 188 | 106.9 | 0.382 | 0.052 | NA | 0.002 | 4.299E-5 | -153.435 | -81.87
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

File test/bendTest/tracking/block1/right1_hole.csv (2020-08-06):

Nr | TID | PID | x [inch] | y [inch] | t [sec] | I [val] | Len [inch] | D2S [inch] | D2R [inch] | D2P [inch] | v [inch/sec] | α [deg] | Δα [deg]
20 | 2 | 32 | 4.258 | 1.788 | 0 | 109.6 | 0 | 0 | NA | NA | NA | NA | NA
21 | 2 | 31 | 4.266 | 1.714 | 1 | 115.6 | 0.075 | 0.075 | NA | 0.075 | 0.075 | -84.408 | NA
22 | 2 | 30 | 4.321 | 1.797 | 2 | 123.3 | 0.174 | 0.063 | NA | 0.1 | 0.1 | 56.227 | 140.636
23 | 2 | 27 | 4.247 | 1.789 | 3 | 124.9 | 0.249 | 0.011 | NA | 0.075 | 0.075 | -173.616 | 130.157
24 | 2 | 28 | 4.251 | 1.758 | 4 | 117.5 | 0.281 | 0.031 | NA | 0.031 | 0.031 | -82.405 | 91.21
25 | 2 | 29 | 4.251 | 1.746 | 5 | 112.7 | 0.292 | 0.043 | NA | 0.011 | 0.011 | -90 | -7.595
26 | 2 | 26 | 4.256 | 1.752 | 15 | 114.5 | 0.3 | 0.036 | NA | 0.008 | 7.717E-4 | 47.726 | 137.726
27 | 2 | 25 | 4.252 | 1.75 | 35 | 116.8 | 0.305 | 0.039 | NA | 0.005 | 2.556E-4 | -156.038 | 156.236
28 | 2 | 24 | 4.244 | 1.758 | 51 | 156.3 | 0.316 | 0.034 | NA | 0.011 | 6.882E-4 | 135 | -68.962
29 | 2 | 23 | 4.253 | 1.758 | 63 | 120.1 | 0.325 | 0.031 | NA | 0.009 | 7.786E-4 | 0 | -135
30 | 2 | 22 | 4.255 | 1.753 | 83 | 117.9 | 0.33 | 0.035 | NA | 0.005 | 2.556E-4 | -66.038 | -66.038
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

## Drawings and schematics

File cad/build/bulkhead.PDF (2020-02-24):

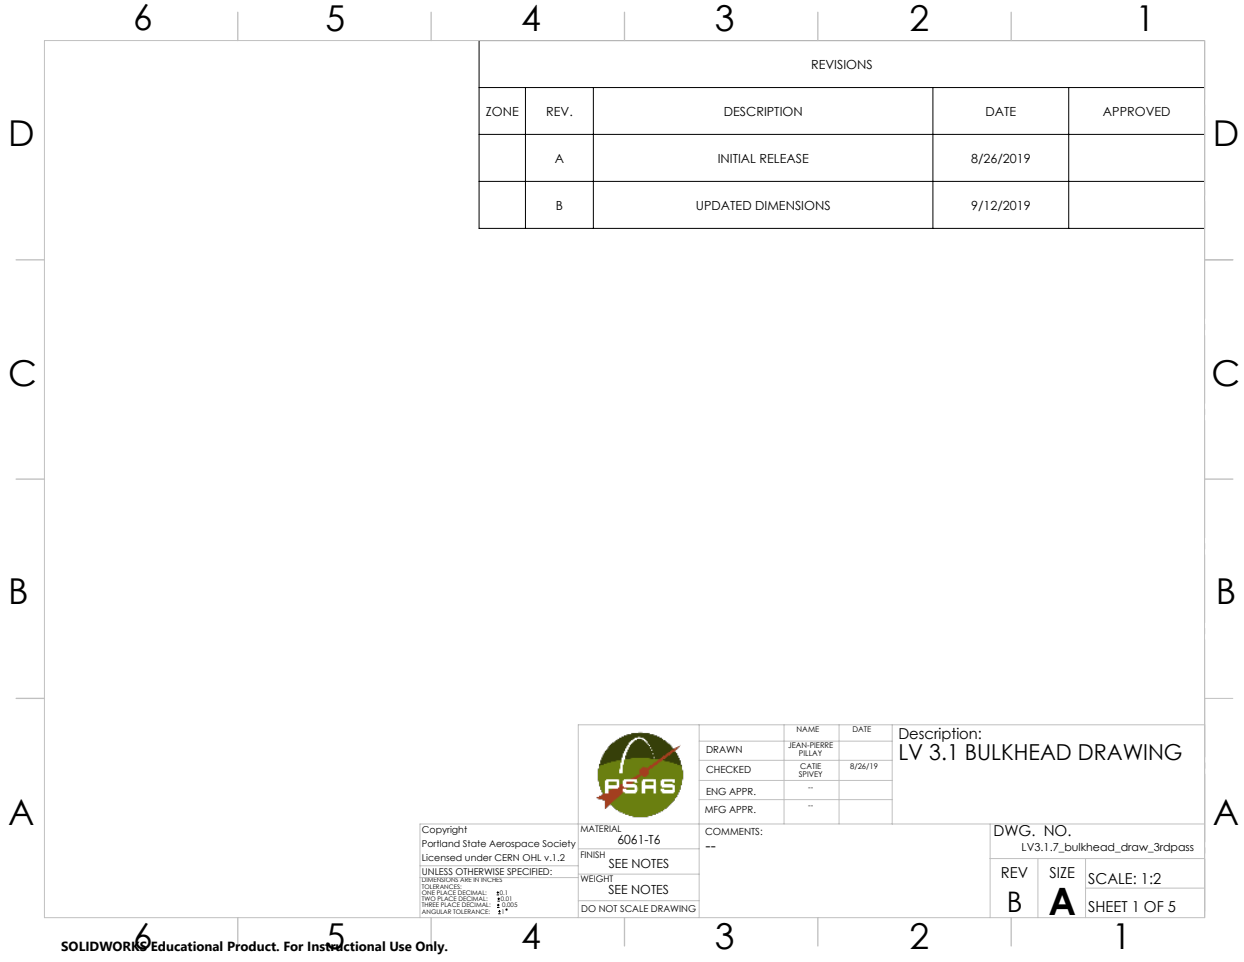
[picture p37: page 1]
ONE PLACE DECIMAL:; TWO PLACE DECIMAL:; THREE PLACE DECIMAL:; ANGULAR TOLERANCE:; SEE NOTES; SCALE: 1:2; DO NOT SCALE DRAWING; SHEET 1 OF 5

REVISIONS

ZONE | REV. | DESCRIPTION | DATE | APPROVED

A | INITIAL RELEASE | 8/26/2019

B | UPDATED DIMENSIONS | 9/12/2019

NAME | DATE | Description: LV 3.1 BULKHEAD DRAWING

DRAWN | JEAN-PIERRE PILLAY
CHECKED | CATIE SPIVEY | 8/26/19
ENG APPR. | --
MFG APPR. | --

Copyright Portland State Aerospace Society Licensed under CERN OHL v.1.2 | MATERIAL 6061-T6 | COMMENTS: -- | DWG. NO. LV3.1.7_bulkhead_draw_3rdpass

UNLESS OTHERWISE SPECIFIED:
DIMENSIONS ARE IN INCHES
TOLERANCES:

SOLIDWORKS Educational Product. For Instructional Use Only.

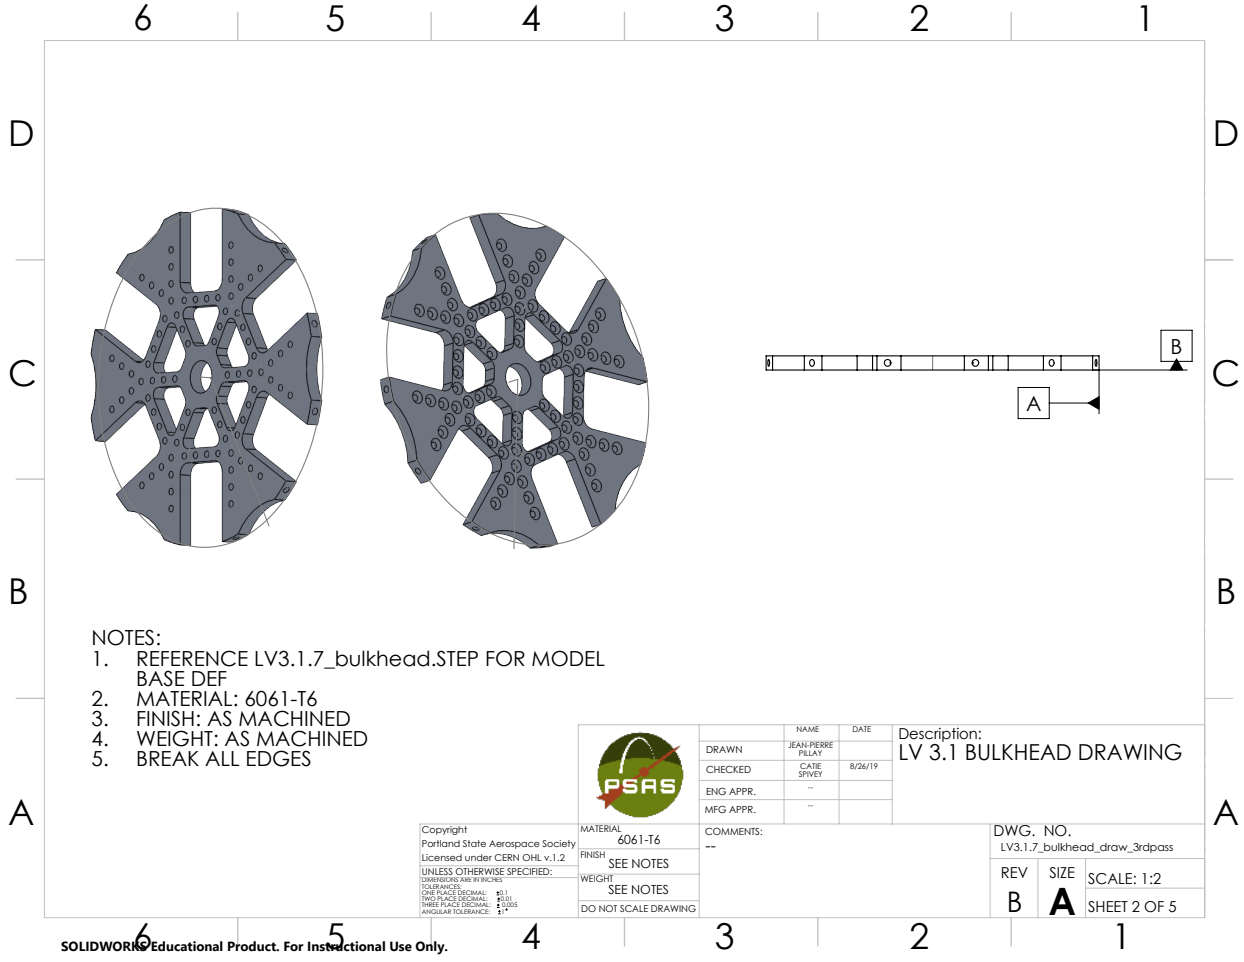
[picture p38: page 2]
SEE NOTES; SCALE: 1:2

NOTES:
1. REFERENCE LV3.1.7_bulkhead.STEP FOR MODEL
BASE DEF
2. MATERIAL: 6061-T6
3. FINISH: AS MACHINED
4. WEIGHT: AS MACHINED
5. BREAK ALL EDGES

NAME | DATE | Description: LV 3.1 BULKHEAD DRAWING

DRAWN | JEAN-PIERRE PILLAY
CHECKED | CATIE SPIVEY | 8/26/19
ENG APPR. | --
MFG APPR. | --

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

UNLESS OTHERWISE SPECIFIED:

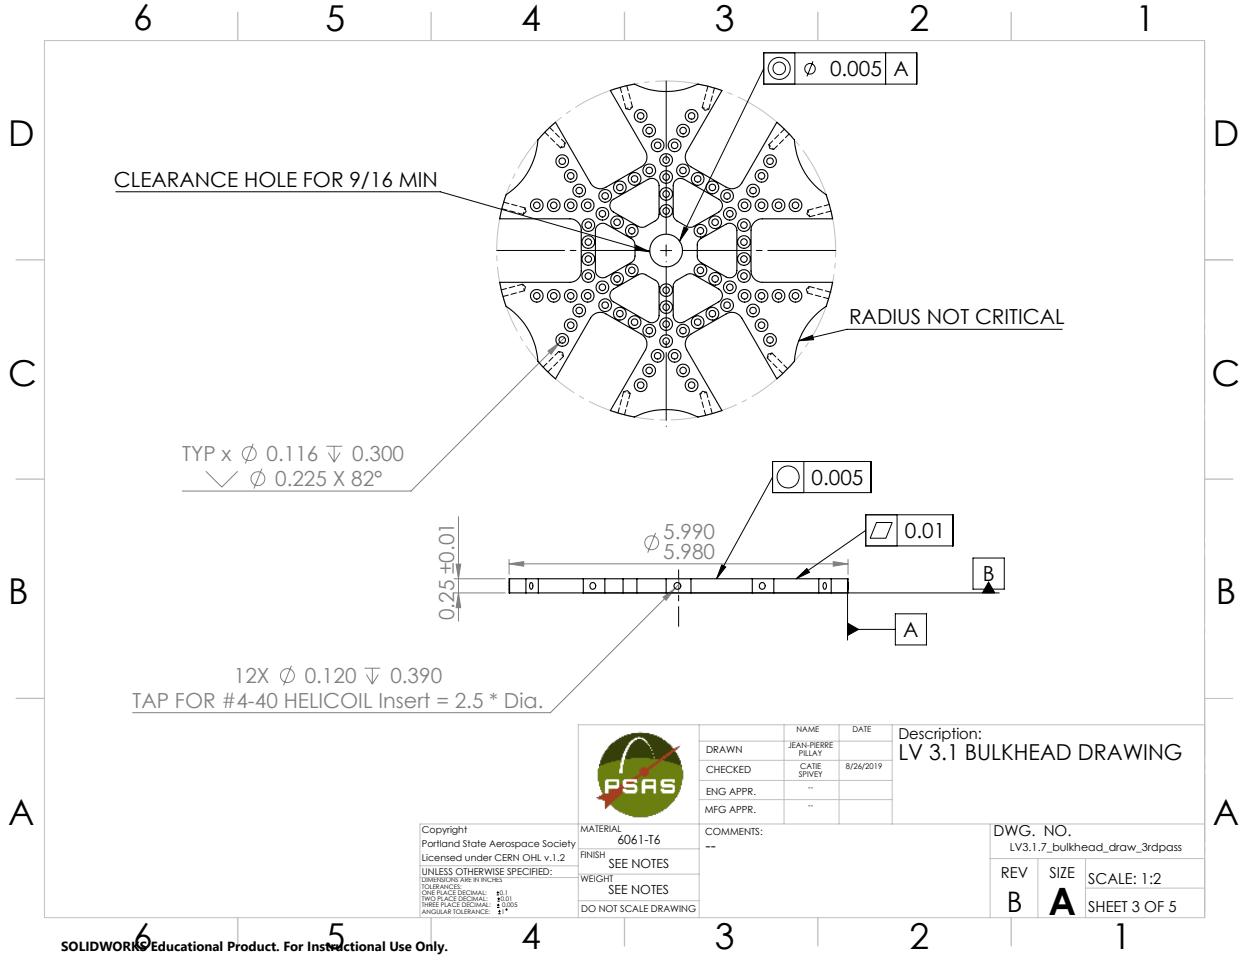
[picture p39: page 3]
TYP x; SEE NOTES; SCALE: 1:2

CLEARANCE HOLE FOR 9/16 MIN

RADIUS NOT CRITICAL

TAP FOR #4-40 HELICOIL Insert = 2.5 * Dia.

NAME | DATE | Description: LV 3.1 BULKHEAD DRAWING

DRAWN | JEAN-PIERRE PILLAY
CHECKED | CATIE SPIVEY | 8/26/2019
ENG APPR. | --
MFG APPR. | --

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

UNLESS OTHERWISE SPECIFIED:

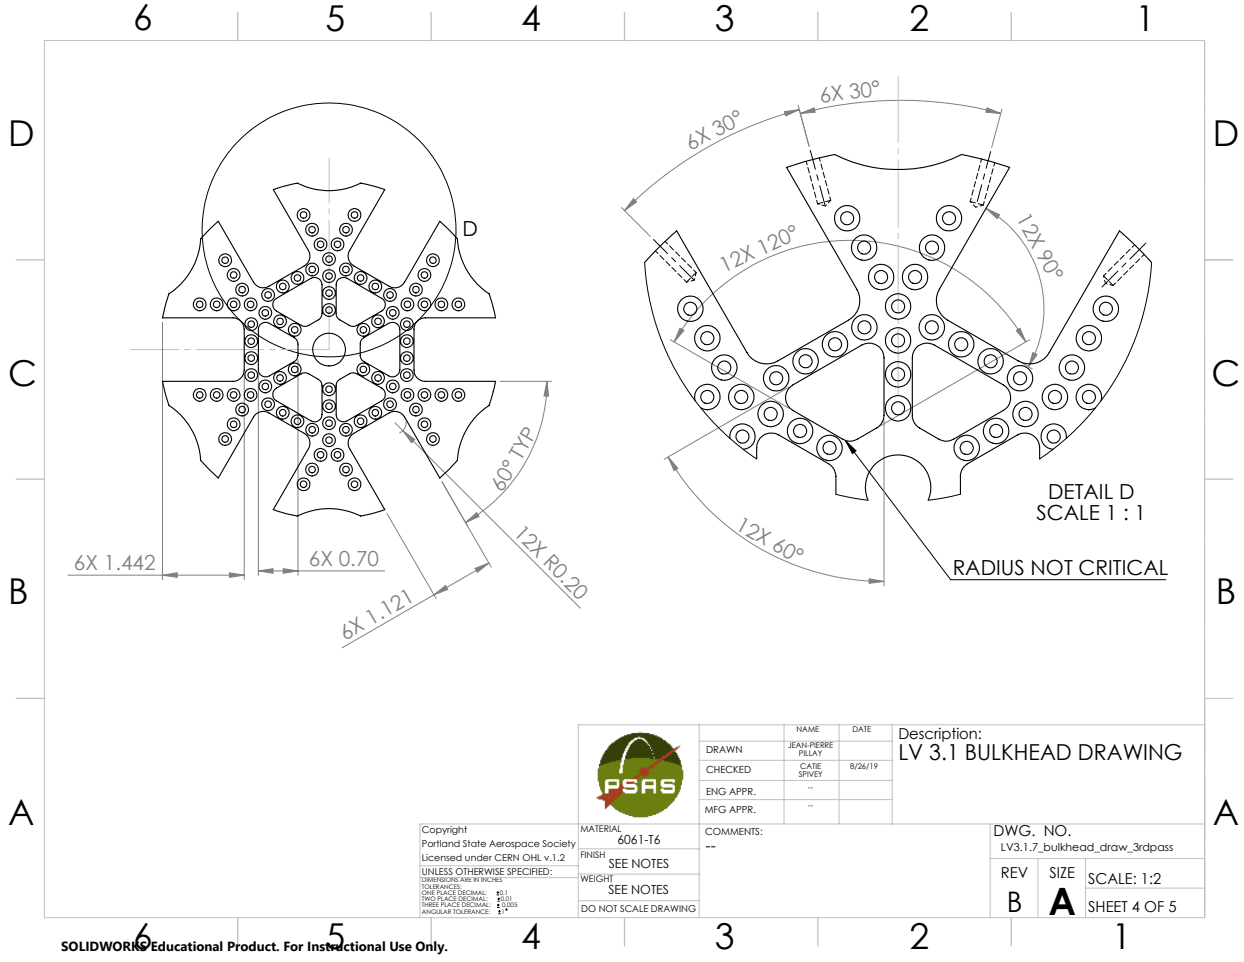
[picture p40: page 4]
60° TYP; DETAIL D SCALE 1 : 1; SEE NOTES; SCALE: 1:2

RADIUS NOT CRITICAL

NAME | DATE | Description: LV 3.1 BULKHEAD DRAWING

DRAWN | JEAN-PIERRE PILLAY
CHECKED | CATIE SPIVEY | 8/26/19
ENG APPR. | --
MFG APPR. | --

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

UNLESS OTHERWISE SPECIFIED:

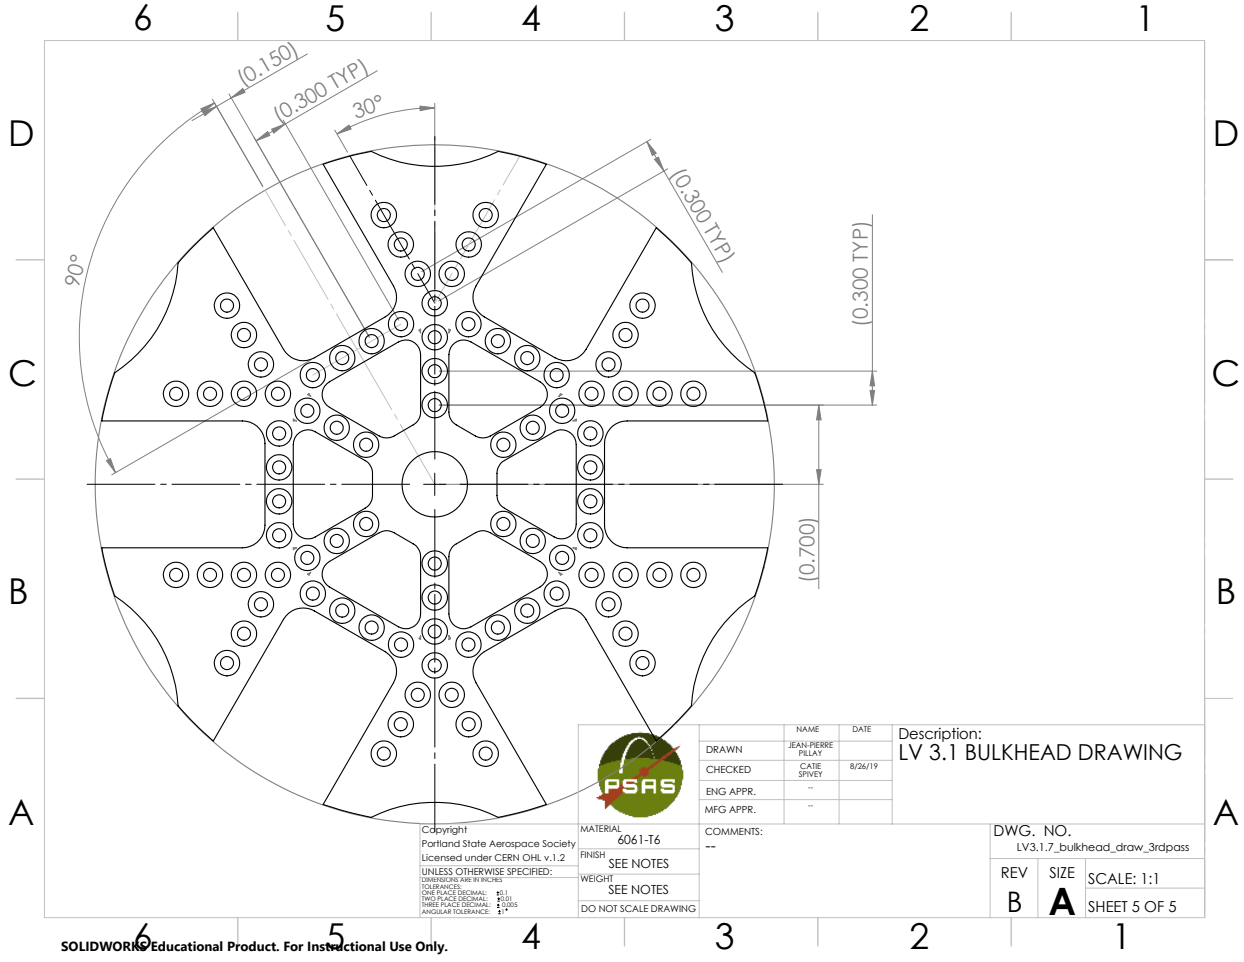
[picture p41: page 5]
(0.300 TYP); SEE NOTES; SCALE: 1:1

NAME | DATE | Description: LV 3.1 BULKHEAD DRAWING

DRAWN | JEAN-PIERRE PILLAY
CHECKED | CATIE SPIVEY | 8/26/19
ENG APPR. | --
MFG APPR. | --

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

UNLESS OTHERWISE SPECIFIED:

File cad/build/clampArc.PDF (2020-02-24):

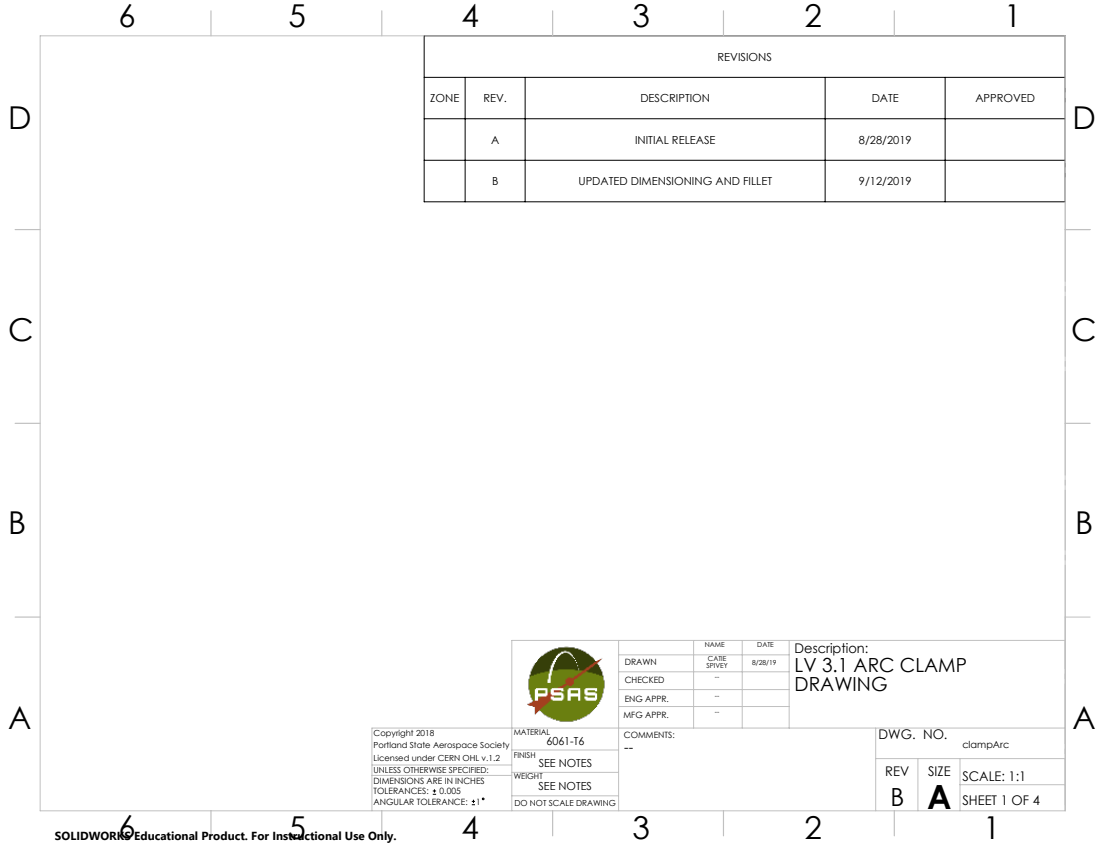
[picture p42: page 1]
SEE NOTES; SCALE: 1:1; DO NOT SCALE DRAWING; SHEET 1 OF 4

REVISIONS

ZONE | REV. | DESCRIPTION | DATE | APPROVED

A | INITIAL RELEASE | 8/28/2019

B | UPDATED DIMENSIONING AND FILLET | 9/12/2019

NAME | DATE | Description: LV 3.1 ARC CLAMP DRAWING

DRAWN | CATIE SPIVEY | 8/28/19
CHECKED | --
ENG APPR. | --
MFG APPR. | --

Copyright 2018 Portland State Aerospace Society Licensed under CERN OHL v.1.2 | MATERIAL 6061-T6 | COMMENTS: -- | DWG. NO. clampArc

UNLESS OTHERWISE SPECIFIED:
DIMENSIONS ARE IN INCHES
TOLERANCES: 0.005
ANGULAR TOLERANCE: 1

SOLIDWORKS Educational Product. For Instructional Use Only.

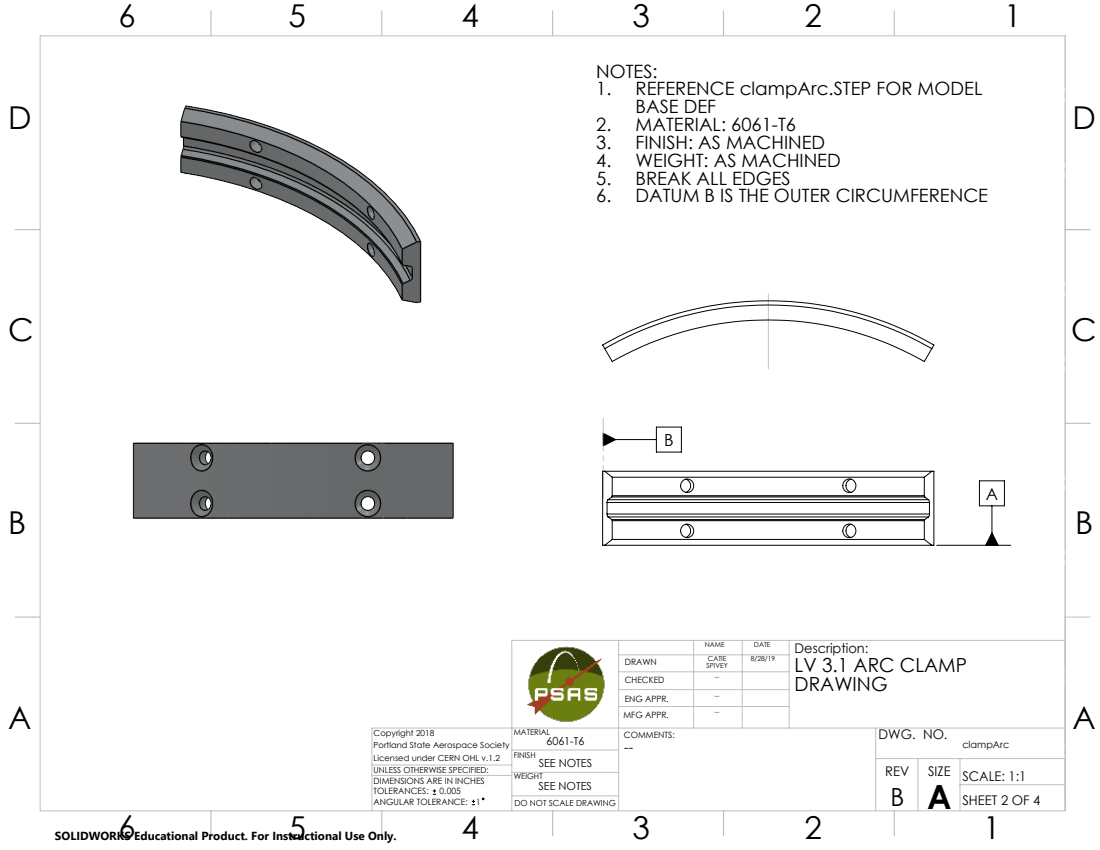
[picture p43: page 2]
SEE NOTES; SCALE: 1:1

NOTES:
1. REFERENCE clampArc.STEP FOR MODEL
BASE DEF
2. MATERIAL: 6061-T6
3. FINISH: AS MACHINED
4. WEIGHT: AS MACHINED
5. BREAK ALL EDGES
6. DATUM B IS THE OUTER CIRCUMFERENCE

NAME | DATE | Description: LV 3.1 ARC CLAMP DRAWING

DRAWN | CATIE SPIVEY | 8/28/19
CHECKED | --
ENG APPR. | --
MFG APPR. | --

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

UNLESS OTHERWISE SPECIFIED:

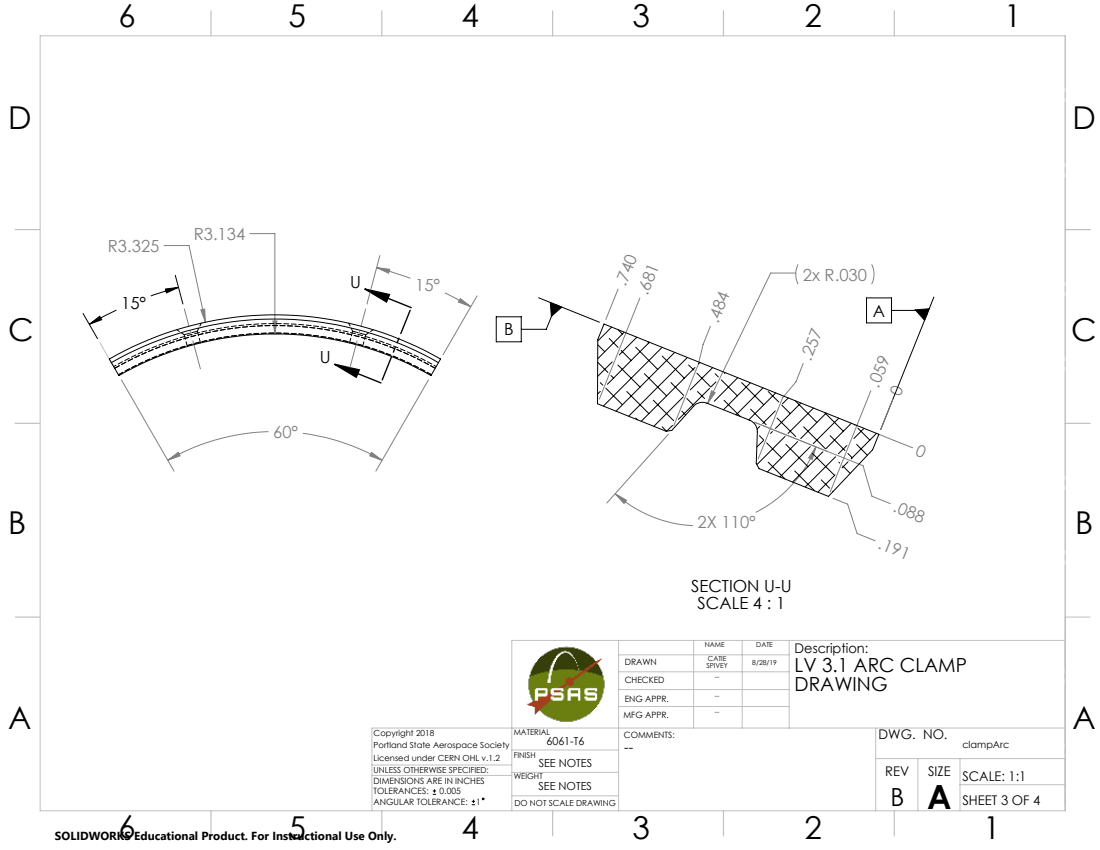
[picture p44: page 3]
SECTION U-U SCALE 4 : 1; SEE NOTES; SCALE: 1:1

NAME | DATE | Description: LV 3.1 ARC CLAMP DRAWING

DRAWN | CATIE SPIVEY | 8/28/19
CHECKED | --
ENG APPR. | --
MFG APPR. | --

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

UNLESS OTHERWISE SPECIFIED:

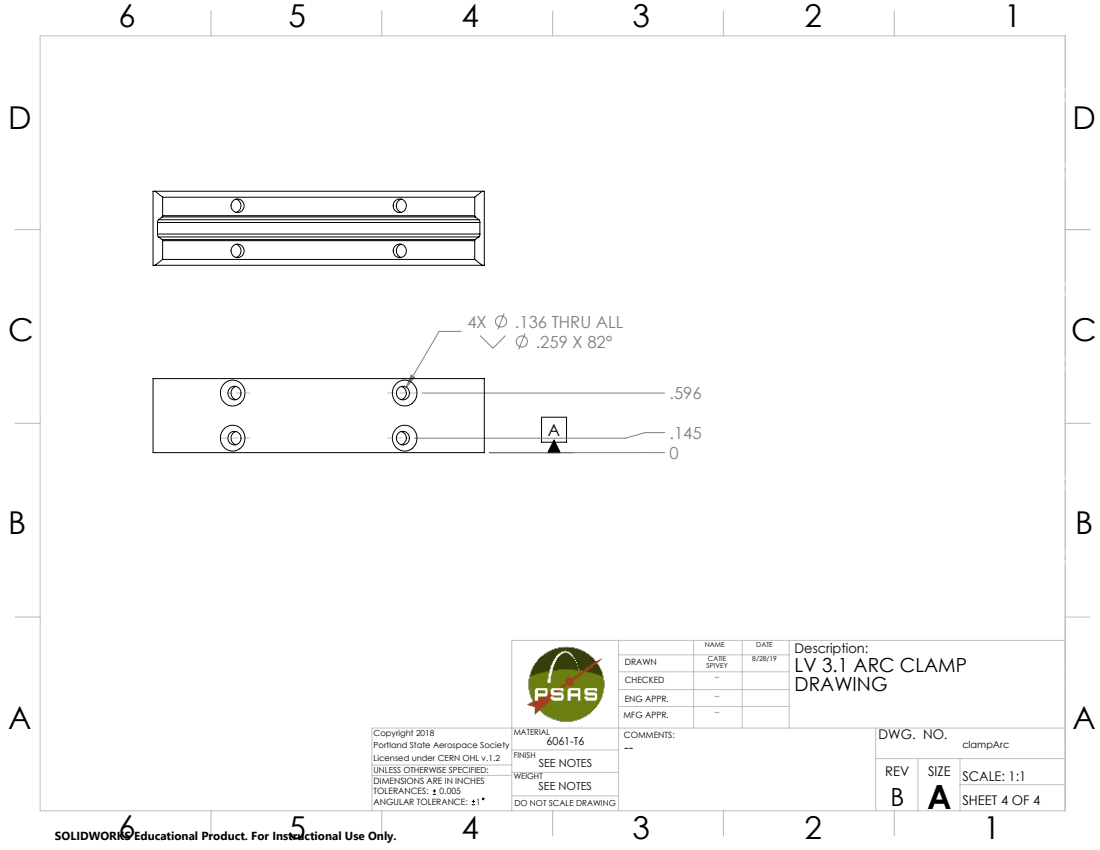
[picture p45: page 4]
.136 THRU ALL; SEE NOTES; SCALE: 1:1

NAME | DATE | Description: LV 3.1 ARC CLAMP DRAWING

DRAWN | CATIE SPIVEY | 8/28/19
CHECKED | --
ENG APPR. | --
MFG APPR. | --

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

UNLESS OTHERWISE SPECIFIED:

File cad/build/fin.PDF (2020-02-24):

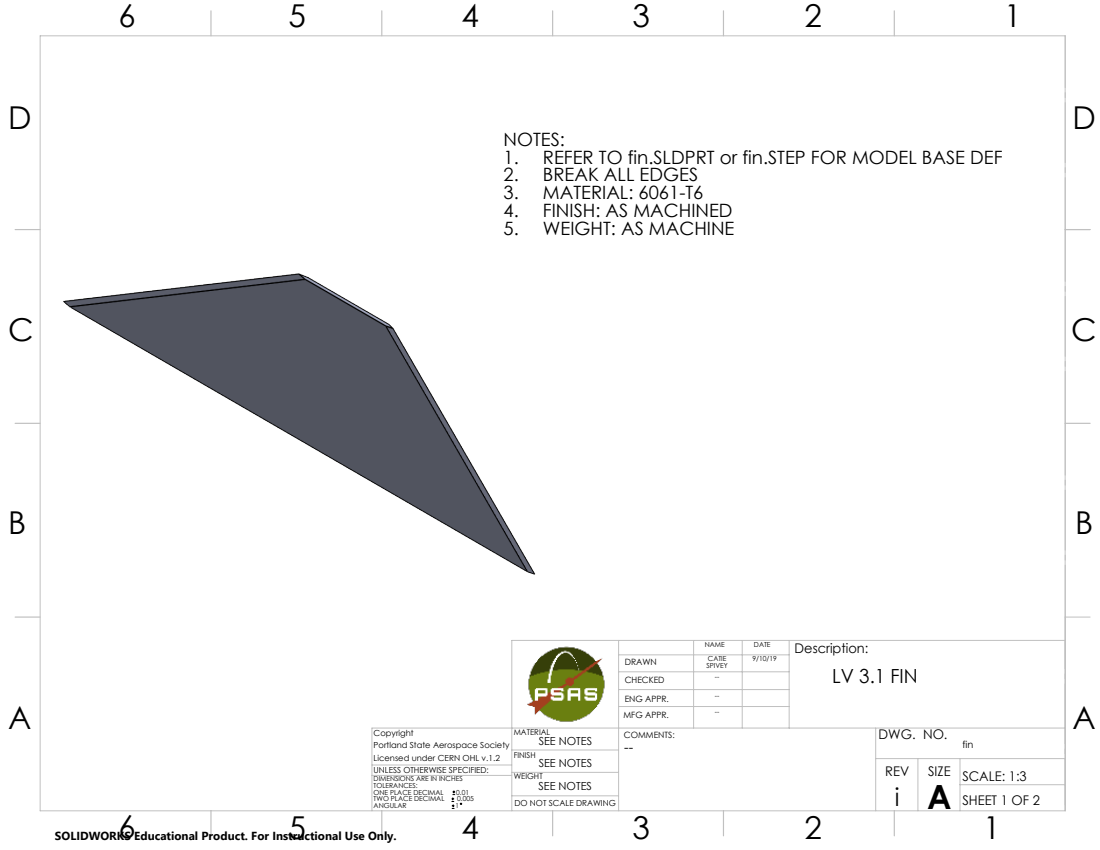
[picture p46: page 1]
ONE PLACE DECIMAL; 0.01 TWO PLACE DECIMAL; SEE NOTES; SCALE: 1:3; DO NOT SCALE DRAWING; SHEET 1 OF 2

NOTES:
1. REFER TO fin.SLDPRT or fin.STEP FOR MODEL BASE DEF
2. BREAK ALL EDGES
3. MATERIAL: 6061-T6
4. FINISH: AS MACHINED
5. WEIGHT: AS MACHINE

NAME | DATE | Description: LV 3.1 FIN

DRAWN | CATIE SPIVEY | 9/10/19
CHECKED | --
ENG APPR. | --
MFG APPR. | --

Copyright Portland State Aerospace Society Licensed under CERN OHL v.1.2 | MATERIAL SEE NOTES | COMMENTS: -- | DWG. NO. fin

UNLESS OTHERWISE SPECIFIED:
DIMENSIONS ARE IN INCHES
TOLERANCES:

SOLIDWORKS Educational Product. For Instructional Use Only.

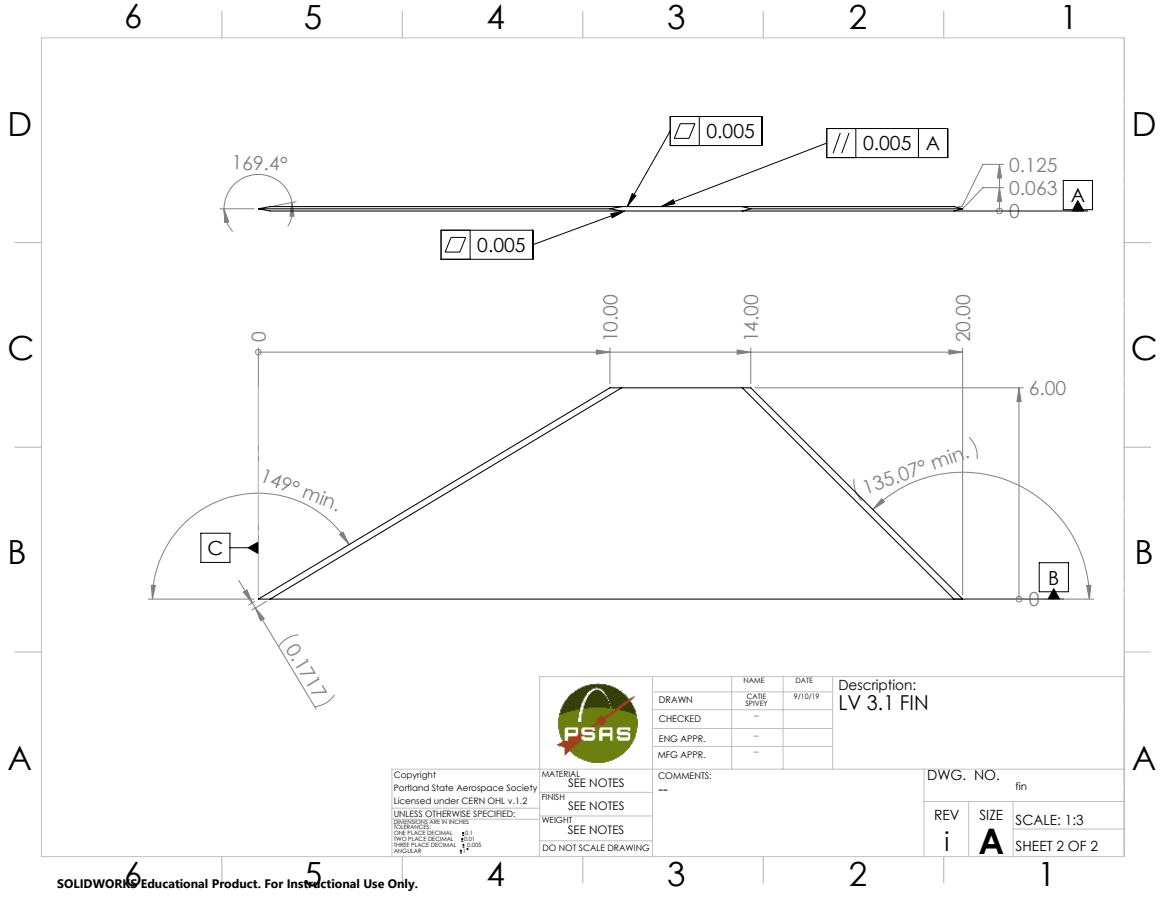
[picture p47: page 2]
149° min.; 135.07° min.; ONE PLACE DECIMAL; TWO PLACE DECIMAL; THREE PLACE DECIMAL; SEE NOTES; SCALE: 1:3; DO NOT SCALE DRAWING; SHEET 2 OF 2

NAME | DATE | Description: LV 3.1 FIN

DRAWN | CATIE SPIVEY | 9/10/19
CHECKED | --
ENG APPR. | --
MFG APPR. | --

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

UNLESS OTHERWISE SPECIFIED:
DIMENSIONS ARE IN INCHES
TOLERANCES:

SOLIDWORKS Educational Product. For Instructional Use Only.

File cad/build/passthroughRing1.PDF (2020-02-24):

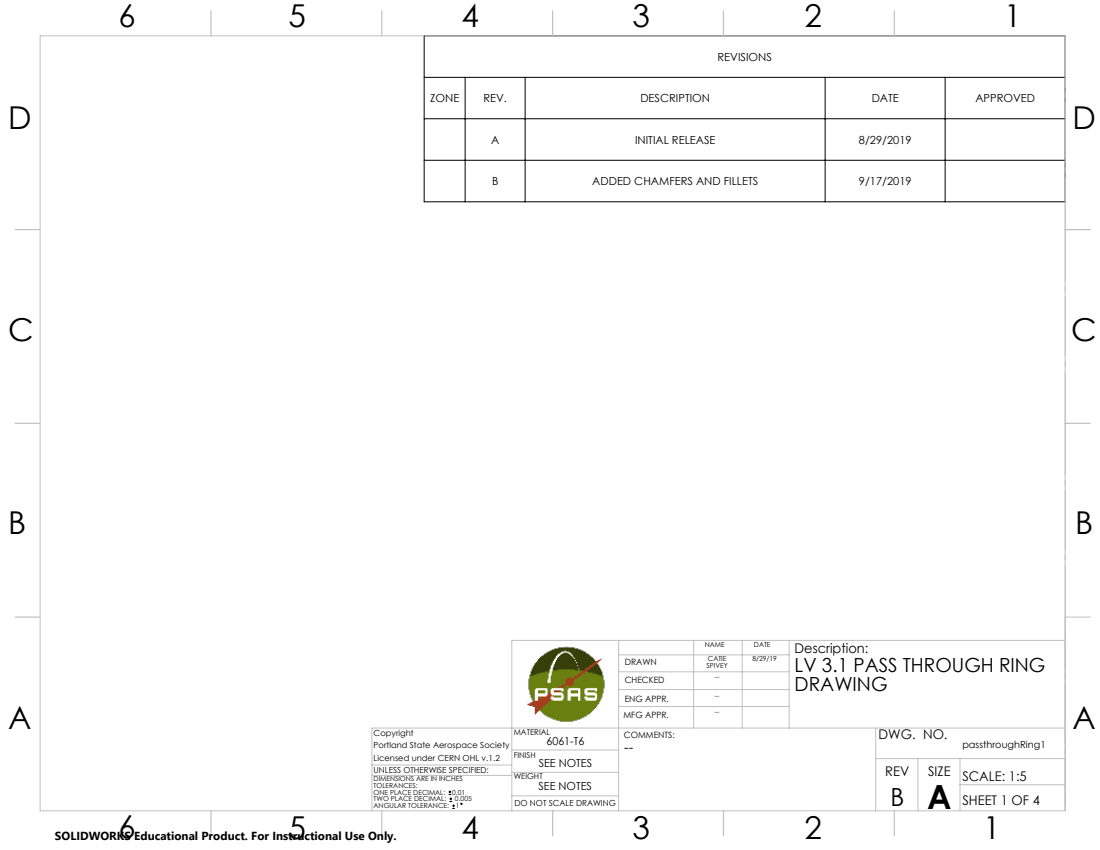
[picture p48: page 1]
SEE NOTES; SCALE: 1:5; DO NOT SCALE DRAWING; SHEET 1 OF 4

REVISIONS

ZONE | REV. | DESCRIPTION | DATE | APPROVED

A | INITIAL RELEASE | 8/29/2019

B | ADDED CHAMFERS AND FILLETS | 9/17/2019

NAME | DATE | Description: LV 3.1 PASS THROUGH RING DRAWING

DRAWN | CATIE SPIVEY | 8/29/19
CHECKED | --
ENG APPR. | --
MFG APPR. | --

Copyright Portland State Aerospace Society Licensed under CERN OHL v.1.2 | MATERIAL 6061-T6 | COMMENTS: -- | DWG. NO. passthroughRing1

UNLESS OTHERWISE SPECIFIED:
DIMENSIONS ARE IN INCHES
TOLERANCES:
ONE PLACE DECIMAL: 0.01
TWO PLACE DECIMAL: 0.005
ANGULAR TOLERANCE: 1

SOLIDWORKS Educational Product. For Instructional Use Only.

SEE NOTES; SCALE: 1:3

NOTES:
1. REFERENCE passthroughRing1.STEP FOR MODEL
BASE DEF
2. MATERIAL: 6061-T6
3. FINISH: AS MACHINED
4. WEIGHT: AS MACHINED

5. BREAK ALL EDGES
6. PART IS SYMMETRICAL ABOUT DATUMS B, AND C

NAME | DATE | Description: LV 3.1 PASS THROUGH RING DRAWING

DRAWN | CATIE SPIVEY | 8/29/19
CHECKED | --
ENG APPR. | --
MFG APPR. | --

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

UNLESS OTHERWISE SPECIFIED:
DIMENSIONS ARE IN INCHES

.116 THRU; .116 THRU ALL; R.1 FOR MACHINING PURPOSES; R3.0 MIN; B SECTION A-A SCALE 1 : 2; 6X .521 MIN; 2X .468 MIN; SECTION B-B; SCALE 1 : 2; 45 CHAMFER FOR MACHINING PURPOSES; SEE NOTES; SCALE: 1:5

ROUND OUTER EDGES

NAME | DATE | Description: LV 3.1 PASS THROUGH RING DRAWING

DRAWN | CATIE SPIVEY | 8/29/19
CHECKED | --
ENG APPR. | --
MFG APPR. | --

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

UNLESS OTHERWISE SPECIFIED:
DIMENSIONS ARE IN INCHES

.089 THRU; SECTION C-C; SEE NOTES; SCALE: 1:2

TAP FOR #4-40 HELICOIL INSERT = 1.0*DIA.

NAME | DATE | Description: LV 3.1 PASS THROUGH RING DRAWING

DRAWN | CATIE SPIVEY | 8/29/19
CHECKED | --
ENG APPR. | --
MFG APPR. | --

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

UNLESS OTHERWISE SPECIFIED:
DIMENSIONS ARE IN INCHES

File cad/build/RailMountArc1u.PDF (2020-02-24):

SEE NOTES; SCALE: 1:1; DO NOT SCALE DRAWING; SHEET 1 OF 4

REVISIONS

ZONE | REV. | DESCRIPTION | DATE | APPROVED

A | INITIAL RELEASE | 8/27/2019

B | UPDATED DIMENSIONING AND FILLET | 9/12/2019

NAME | DATE | Description: LV 3.1 LAUNCH LUG DRAWING

DRAWN | CATIE SPIVEY | 8/26/19
CHECKED | --
ENG APPR. | --
MFG APPR. | --

Copyright Portland State Aerospace Society Licensed under CERN OHL v.1.2 | MATERIAL 6061-T6 | COMMENTS: -- | DWG. NO. RailMountArc1u

UNLESS OTHERWISE SPECIFIED:
DIMENSIONS ARE IN INCHES
TOLERANCES: 0.005
ANGULAR TOLERANCE: 1

SOLIDWORKS Educational Product. For Instructional Use Only.

SEE NOTES; SCALE: 3:2

NOTES:
1. REFERENCE RailMountArc1u.STEP FOR MODEL
BASE DEF
2. MATERIAL: 6061-T6
3. FINISH: AS MACHINED
4. WEIGHT: AS MACHINED
5. BREAK ALL EDGES
6. DATUM B IS THE OUTER CIRCUMFERENCE

NAME | DATE | Description: LV 3.1 LAUNCH LUG DRAWING

DRAWN | CATIE SPIVEY | 8/26/19
CHECKED | --
ENG APPR. | --
MFG APPR. | --

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

UNLESS OTHERWISE SPECIFIED:

2X 30° max.; 0.191 max.; SECTION A-A SCALE 5 : 1; SEE NOTES; SCALE: 1:1

NAME | DATE | Description: LV 3.1 LAUNCH LUGS DRAWING

DRAWN | CATIE SPIVEY | 8/26/19
CHECKED | --
ENG APPR. | --
MFG APPR. | --

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

UNLESS OTHERWISE SPECIFIED:

0.136 THRU ALL; SECTION B-B; SEE NOTES; SCALE: 3:2

TAP FOR M6x1.0 HELICOIL

RADIUS NOT CRITICAL

NAME | DATE | Description: LV 3.1 LAUNCH LUG DRAWING

DRAWN | CATIE SPIVEY | 8/26/19
CHECKED | --
ENG APPR. | --
MFG APPR. | --

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

UNLESS OTHERWISE SPECIFIED:

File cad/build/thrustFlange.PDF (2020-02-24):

SEE NOTES; SCALE: 1:1; DO NOT SCALE DRAWING; SHEET 1 OF 4

REVISIONS

ZONE | REV. | DESCRIPTION | DATE | APPROVED

A | INITIAL RELEASE | 8/27/2019

B | UPDATED DIMENSIONING | 9/12/2019

NAME | DATE | Description: LV 3.1 THRUST FLANGE DRAWING

DRAWN | CATIE SPIVEY | 8/27/19
CHECKED | --
ENG APPR. | --
MFG APPR. | --

Copyright Portland State Aerospace Society Licensed under CERN OHL v.1.2 | MATERIAL 6061-T6 | COMMENTS: -- | DWG. NO. thrustFlange

UNLESS OTHERWISE SPECIFIED:
DIMENSIONS ARE IN INCHES
TOLERANCES: 0.005
ANGULAR TOLERANCE: 1

SOLIDWORKS Educational Product. For Instructional Use Only.

SEE NOTES; SCALE: 1:1

NOTES:
1. REFERENCE thrustFlange.STEP FOR MODEL
BASE DEF
2. MATERIAL: 6061-T6
3. FINISH: AS MACHINED
4. WEIGHT: AS MACHINED
5. BREAK ALL EDGES

NAME | DATE | Description: LV 3.1 THRUST FLANGE DRAWING

DRAWN | CATIE SPIVEY | 8/27/19
CHECKED | --
ENG APPR. | --
MFG APPR. | --

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

UNLESS OTHERWISE SPECIFIED:

SECTION D-D; SEE NOTES; SCALE: 1:2

TAP FOR #4-40 HELICOIL Insert = 1.0 * Dia.

NAME | DATE | Description: LV 3.1 THRUST FLANGE DRAWING

DRAWN | CATIE SPIVEY | 8/26/19
CHECKED | --
ENG APPR. | --
MFG APPR. | --

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

UNLESS OTHERWISE SPECIFIED:

R0.130 min.; 6X 0.250 min.; SECTION C-C; SEE NOTES; SCALE: 1:2

NAME | DATE | Description: LV 3.1 THRUST FLANGE DRAWING

DRAWN | CATIE SPIVEY | 8/26/19
CHECKED | --
ENG APPR. | --
MFG APPR. | --

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

UNLESS OTHERWISE SPECIFIED:

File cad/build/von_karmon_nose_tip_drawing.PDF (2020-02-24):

SEE NOTES; SCALE: 1:1; DO NOT SCALE DRAWING; SHEET 1 OF 4

REVISIONS

ZONE | REV. | DESCRIPTION | DATE | APPROVED

A6 | A | INITIAL RELEASE | 4/12/2017

B | UPDATED FORMATTING | 12/8/2019

NAME | DATE | Description: LV3.1 NOSECONE TIP FOR LAUNCH 14

DRAWN | JOE SHIELDS | 4/12/2017
CHECKED | EMILIO GIZZI | 12/8/2019
ENG APPR. | --
MFG APPR. | --

Copyright 2018 Portland State Aerospace Society Licensed under CERN OHL v.1.2 | MATERIAL 6061-T6 | COMMENTS: | DWG. NO. von_karmon_nose_tip2

UNLESS OTHERWISE SPECIFIED:
DIMENSIONS ARE IN INCHES
TOLERANCES:
ANGULAR: MACH 1° BEND 1°
ONE PLACE DECIMAL .1
TWO PLACE DECIMAL .01
THREE PLACE DECIMAL .001

SOLIDWORKS Educational Product. For Instructional Use Only.

SEE NOTES; SCALE: 1:1

NOTES
1. REFERENCE
von_karmon_nose_tip2.SLDDRW FOR
MODEL BASE DEF
2. MATERIAL 6061-T6
3. FINISH: AS MACHINED
4. WEIGHT: AS MACHINED
5. BREAK ALL EDGES

NAME | DATE | Description: LV3.1 NOSECONE TIP FOR LAUNCH 14

DRAWN | JOE SHIELDS | 4/12/2017
CHECKED | EMILIO GIZZI | 12/8/2019
ENG APPR. | --
MFG APPR. | --

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

UNLESS OTHERWISE SPECIFIED:
DIMENSIONS ARE IN INCHES
TOLERANCES:
ANGULAR: MACH 1° BEND 1°

BACK VIEW; SECTION A-A; SEE NOTES; SCALE: 1:1

TAP FOR 9/16-12 HELICOIL Insert = 1.0 * Dia. 1.69

NAME | DATE | Description: LV3.1 NOSECONE TIP FOR LAUNCH 14

DRAWN | JOE SHIELDS | 4/12/2017
CHECKED | EMILIO GIZZI | 12/8/2019
ENG APPR. | --
MFG APPR. | --

UNLESS OTHERWISE SPECIFIED: | MATERIAL 6061-T6 | COMMENTS: | DWG. NO. von_karmon_nose_tip2

DIMENSIONS ARE IN INCHES
TOLERANCES:
ANGULAR: MACH 1° BEND 1°

DETAIL B SCALE 4 : 1; DETAIL C SCALE 4 : 1; SEE NOTES SEE NOTES; SCALE: 1:1

NAME | DATE | Description: LV3.1 NOSECONE TIP FOR LAUNCH 14

DRAWN | JOE SHIELDS | 4/12/2017
CHECKED | EMILIO GIZZI | 12/8/2019
ENG APPR. | --
MFG APPR. | --

UNLESS OTHERWISE SPECIFIED: | MATERIAL 6061-T6 | COMMENTS: | DWG. NO. von_karmon_nose_tip2

DIMENSIONS ARE IN INCHES
TOLERANCES:
ANGULAR: MACH 1° BEND 1°

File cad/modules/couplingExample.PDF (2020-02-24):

SECTION B-B; SECTION A-A; UNLESS OTHERWISE SPECIFIED:; DO NOT SCALE DRAWING; SHEET 1 OF 3; SCALE: 1:2 --; DWG. NO.; SIZE; Finish; AS MACHINED; TOLERANCES: 0.127

NAME | DATE | Description: Example of the LV3.1 coupling

DRAWN | Joe S. | 11/8/2018
CHECKED | --
MFG APPR. | --

Copyright 2018 Portland State Aerospace Society Licensed under CERN OHL v.1.2 | | ENG APPR. | --

Material DIMENSIONS ARE IN MILLIMETERS

SOLIDWORKS Educational Product. For Instructional Use Only.

DETAIL C A; SCALE 2 : 1

NAME | DATE | Description: Example of the LV3.1 coupling

DRAWN | Joe S. | 11/8/2018
CHECKED | --
MFG APPR. | --
COMMENTS: -- | i REV DWG. NO. | SIZE

Copyright 2018 Portland State Aerospace Society Licensed under CERN OHL v.1.2 | | ENG APPR. | --

UNLESS OTHERWISE SPECIFIED: | 6061-T6 | | --

DETAIL D A; SCALE 2 : 1

NAME | DATE | Description: Example of the LV3.1 coupling

DRAWN | Joe S. | 11/8/2018
CHECKED | --
MFG APPR. | --
COMMENTS: -- | i REV DWG. NO. | SIZE

Copyright 2018 Portland State Aerospace Society Licensed under CERN OHL v.1.2 | | ENG APPR. | --

UNLESS OTHERWISE SPECIFIED: | 6061-T6 | | --

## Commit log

2018-06-12 wedge-clamp idea for LV3.1 coupling rings
    [M3x0.5x8_CSK_torxPlus_94414A713_ALLOY STEEL TORX FLAT HEAD SCREWS.SLDPRT, clampArc.SLDPRT, compositeInnerSleeve.SLDPRT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]
2018-06-13 male/female rings with mating cones
    [clampArc.SLDPRT, couplingDefinition.SLDPRT, moduleRing.SLDPRT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]
2018-06-23 Incorporated William Winters' changes
    - Switched to M4 screws
    - Coulnd't really make countersunk cap-head screws work gracefully, so went with 90 deg CSK
    - Beef'd up the landing area that the screws thread into, to avoid threading through an angled surface
    - Changed the wedge angle to 15 degrees from 30 to increase mechanical advantage
    [M4x0.7x8_CSK_hex_91294A188_BLACK ALLOY STEEL FLAT-HEAD SOCKET CAP SCREW.SLDPRT, clampArc.SLDPRT, compositeLapRing.SLDPRT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]
2018-06-23 Renamed parts to match the lack of male/female versions
    [couplingExample.SLDASM, module24.SLDASM, moduleRing.SLDPRT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]
2018-07-28 hole callouts for coupling ring and clamps
    These drawings just show the holes and bounding boxes.
    IMPORTANT: The hole callouts needed to be set manually for some reason.
    SW may not like threaded features being put through the "import part"
    feature...
    [clampArc.SLDDRW, moduleRing.SLDDRW]
2018-08-01 switched M4 fasteners for 4-40 helicoil
    [clampArc.SLDDRW, clampArc.SLDPRT, couplingDefinition.SLDPRT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]
2018-08-01 re-optimized dimensions for 4-40 fasteners
    [4-40x0.3125_82degCSK_flatHex_91253A107_ALLOY STEEL FLAT-HEAD SOCKET CAP SCREW.SLDPRT, 4-40x0.375_82degCSK_flatHex_91253A108_ALLOY STEEL FLAT-HEAD SOCKET CAP SC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]
2018-08-08 Committing Georges' file for nosecone mold manufacture parts
    [HalfMoldAssembly.SLDASM]
2018-08-08 Saving Georges' experimental files stored on the EPL CAD station
    [Georges_Experimental_Nosecone.SLDPRT, Georges_Experimental_Nosecone_Half_Mold.SLDPRT, Georges_Experimental_Nosecone_Mandrel_Basis_shape.SLDPRT]
2018-08-19 Added registration holes to the mandrel mold!
    [Georges_Experimental_Nosecone_Half_Mold.SLDPRT, HalfMoldAssembly.SLDASM]
2018-08-26 Removed pour-side overhang, added centering rod support backside clearance, added new fillets, set foam block thickness to 4 inches, completely redid all mating and fixed all errors.
    [Georges_Experimental_Nosecone_Half_Mold.SLDPRT, Georges_Experimental_Nosecone_Mandrel_Basis_shape.SLDPRT, HalfMoldAssembly.SLDASM]
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2018-11-09 drawing showing how the couplings work
    [couplingExample.SLDASM, couplingExample.SLDDRW]
2019-01-23 Added New Layup Templates
    Added cad files for the new layup templates for the lv3.1 4-layer module, along with a readme file describing naming conventions.
    These templates are eventually going to be lasercut from acrylic to assist in cutting the carbon fiber and the nomex in the layup process.
    [T-B-IC.SLDPRT, T-B-NO.SLDPRT, T-B-OC.SLDPRT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]
2019-02-04 created the model of the motor casing
    I tried to specify the mass and CoM. Fudging the density and adding an
    internal cavity would be a way to do it, if we really need to. The
    "official" way to do it is with a design table. However, that feature on
    SW is actually... an Excel integration. So, nope.
    [motor_Cesaroni.SLDPRT]
2019-02-22 i just changed the tolerances for the module ring drawing and pdf
    [moduleRing.SLDDRW]
2019-03-01 changed tolerances again
    [moduleRing.SLDDRW, moduleRing.SLDPRT]
2019-03-01 Made assembly and non-virtual parts describing placement and dimensions of D nut relative to other layup components
    [Georges_Experimental_Nosecone_Half_Mold.SLDPRT, Georges_Experimental_Nosecone_Mandrel_Basis_shape.SLDPRT, HalfMoldAssembly.SLDASM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]
2019-03-01 Final tolerance adjustment, changed global tolerance from 0.01in to 0.005in
    [moduleRing.SLDDRW]
2019-03-02 Created single clamp arc rail lug mount
    [RailMountArc1u.SLDPRT]
2019-04-01 Updated Template files with more legible text
    [T-B-IC.SLDPRT, T-B-NO.SLDPRT, T-B-OC.SLDPRT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]
2019-04-03 Corrected Template folder name
    [T-B-IC.SLDPRT, T-B-NO.SLDPRT, T-B-OC.SLDPRT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]
2019-04-07 new drawing for moduleRing
    [moduleRing_redo.SLDDRW]
2019-04-07 new drawing for moduleRing, try 2
    [moduleRing_redo.SLDDRW]
2019-04-19 Added Adams launch rail clamp to repo
    [RailMountArc1u.SLDPRT]
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2019-05-18 Created Fin Can Layup System
    [Bracket Alignment Surfaces.SLDDRW, Bracket Alignment Surfaces^Tip To Tip Jig.sldprt, Bracket Press.SLDDRW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]
2019-05-26 fixed thrust plate
    [couplingDefinition.SLDPRT, thrustPlate.SLDPRT]
2019-05-27 Created alignment jig / nostril spider
    [NostrilSpider.SLDASM]
2019-05-27 Update nostril spider hole size, make part independent.
    [NostrilSpider.SLDASM, NostrilSpider.SLDPRT]
2019-05-31 fixed thrust flange
    [thrustFlange.SLDPRT, thrustPlate.SLDPRT]
2019-05-31 Add mounting holes to thrust flange
    [FlangeAndArcAssem.SLDASM, clampArc.SLDPRT, thrustFlange.SLDPRT]
2019-06-01 Created drawing for Rail Mount Arc
    [RailMountArc1u.SLDDRW]
2019-07-19 adding prototype of 120 degree alignment fixture
    [Fin Can Alignment Accessory.SLDPRT]
2019-07-19 Updated the Nostril Spider to include two flat portions on up-side, down-side for checking the alignment of the spider itself. Also reduced fillet complexity for cleaner print
    [NostrilSpider.SLDASM, NostrilSpider.SLDPRT]
2019-07-21 Added new fin frame design, matching latest math for fin flutter.
    [fin.SLDPRT]
2019-07-22 Created transition ring with two configurations, one with notch, one without.
    [TransitionRing.SLDPRT]
2019-07-26 fixed center hole callout
    [RailMountArc1u.SLDDRW, RailMountArc1u.SLDPRT]
2019-08-02 More modifications to Rail Mount stuff
    [RailMountArc1u.SLDDRW, RailMountArc1u.SLDPRT]
2019-08-02 Updated Fin Alignment Insert
    [Fin Can Alignment Accessory.SLDPRT]
2019-08-02 Pushing Jean-Pierre's Snowflake bulkhead design.
    [LV3.1.7_bulkhead.SLDPRT, LV3.1.7_bulkhead_draw_3rdpass.SLDDRW]
2019-08-11 Created Drawing for Thrust Flange
    [thrustFlange.SLDDRW]
2019-08-18 Final tweaks to thrust flange drawing
    [thrustFlange.SLDDRW]
2019-08-22 Created new fin design with proper mach math. Added STEP, .pdfs for all parts needing to be machined pronto.
    [LV3.1.7_bulkhead.STEP, RailMountArc1u.STEP, fin.SLDDRW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]
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2019-09-01 updated thrust flange pdf to include a note
    [thrustFlange.SLDDRW]
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2019-09-13 updated parts and drawings per western precision notes
    [LV3.1.7_bulkhead_draw_3rdpass.SLDDRW, RailMountArc1u.SLDDRW, RailMountArc1u.SLDPRT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]
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
